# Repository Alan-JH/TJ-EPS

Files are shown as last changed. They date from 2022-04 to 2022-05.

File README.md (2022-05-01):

# TJ-EPS
Custom Battery and EPS for 2-3U Cubesat. Designed to be versatile, and to be implemented on TJ-iSPIN

Heavily inspired by the Clydespace 3G EPS, but not as expensive, and with some improvements.

## Battery
2P2S setup with 3500mAh 18650 Li-Ion cells. Voltage range from 6 to 8.4V.

Series charge balancing using BQ29209

2 Inhibits (1x ground disconnect, 1x positive disconnect)

7A Polyfuse, 8.4V input OVP, 8A Bidirectional momentary OCP/SCP

Ideal Diode with two more positive disconnect inhibits to EPS regulator input, UVP which disconnects at 6.2V falling and re-enables at 7V

One positive disconnect inhibit between EPS charge output and battery

Battery heaters and temperature telemetry to keep them above 0 deg C

Telemetry IC including Voltage, Current, SOC Charge Integration, Temperatures, and Heater control. Watchdog timer to prevent latchup.

## EPS
VBAT, 5V, 3.3V bus outputs, each with latching current limit (3A, 3A, and 5A respectively), voltage and current telemetry.

10 switchable voltage outputs, each with current and voltage telemetry, with voltage selectable between 3.3V, 5V, and BATV by jumper

Telemetry IC including all voltage and current telemetry, board temperature telemetry, and solar regulator telemetry. Watchdog timer to prevent latchup.

#### Solar Daughterboard
Daughterboard which attaches on top of the main EPS stack board.

4 solar input maximum power point tracking regulators, with two connectors each (intended for panels on opposite sides of the satellite or panels guaranteed equal sunlight).

Solar input range from 9V to 26V. Includes series diode protection on each connector. LT3652 regulators each provide up to 2A battery charging output, with 8.27V float voltage. 

Maximum power point tracking voltage settable by trim potentiometer (MUST BE SET BEFORE LAUNCH)

Input current telemetry for each individual connector, input voltage telemetry for each regulator, and output voltage and current telemetry.

## Component selection
Most components are AEC-Q100/Q101/Q200 Automotive qualified. A few important components are not, by necessity due to the chip shortage. Battery cells must be tested in house, but should be selected by brands commonly used in cubesats such as LG and Panasonic. The boards are to be tested with vibration, and vacuum with temperature cycle individually.

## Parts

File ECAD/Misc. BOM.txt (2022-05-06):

10uH: https://www.mouser.com/ProductDetail/Kyocera-AVX/LMLP07A7M100DTAS?qs=BgMWa3ErCfy790mwccrPYw%3D%3D
10uH alternate: https://www.mouser.com/ProductDetail/ABRACON/ASPI-0630HI-100M-T15?qs=bWAYEm3xoCYvNdiREkchng%3D%3D

3.3uH: https://www.mouser.com/ProductDetail/ABRACON/ASPI-0630LR-3R3M-T15?qs=bWAYEm3xoCb65F4PqHLU5A%3D%3D
3.3uH alternate: https://www.mouser.com/ProductDetail/ABRACON/ASPI-0630HI-3R3M-T15?qs=bWAYEm3xoCYwUcwgROPtBA%3D%3D

4.7uH: https://www.mouser.com/ProductDetail/ABRACON/ASPI-0630LR-4R7M-T15?qs=bWAYEm3xoCYVuRmkzS1c6A%3D%3D

33uH: https://www.mouser.com/ProductDetail/Coilcraft/XAL6060-333MEC?qs=lc2O%252BfHJPVZnUE%252BpAAaLKQ%3D%3D

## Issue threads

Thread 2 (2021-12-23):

MPPT Tracking Controller doesn't have ADC input from telemetry

Alan-JH, 2021-12-23:
Controller needs to have access to voltage and current telemetry to calculate a maximum power point

Closed 2021-12-24.

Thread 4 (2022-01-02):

Schematic TODO

Alan-JH, 2022-01-02:
- [x] Implement solar panel telemetry on separable module
- [x] Implement telemetry ADC and controls
- [x] Implement bus reset timer
- [x] Implement overcurrent retry timer
- [x] Implement STM32 Watchdog timer
- [x] Implement USB charge to MPPT4 with LTC4412
- [x] Refine component selection for Buck and Boost controllers in PCM
- [x] Make cell protections separable
- [x] Add sheet comments
- [x] Redundant capacitors (specify in component selection)

Closed 2022-01-31.

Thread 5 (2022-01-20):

Battery cell reselection

Alan-JH, 2022-01-20:
18650s with holders are too physically long
-Spot weld 18650 (High density, but impossible to safely remove cells after integration)
-18500 w/ holders (Low density, but easy to remove cells after integration)
-Pouch cell on stacked boards (Higher cost, harder to spec, and extremely similar to clydespace batt, but customizable cell protection and removeable, and denser than cylindrical cells)

Closed 2022-01-28.

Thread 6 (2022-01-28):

Consider removing destructive OVP

Alan-JH, 2022-01-28:
Semidestructive OVP involves shorting the +batt to ground in order to trigger a polyfuse, and is only a redundancy in case the charge OVP protection earlier fails.

Alan-JH, 2022-01-31:
Added redundant mosfets, and closing this for now

Closed 2022-01-31.

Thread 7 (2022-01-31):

Consolidate parts

Alan-JH, 2022-01-31:
Try to find lower part count solutions for common sub-components such as current sense and PMOS drivers. There are too many components and too little space to put them.

Alan-JH, 2022-01-31:
Going to replace LT6106 with INA180; about half the cost, more available, and less part usage

Closed 2022-03-28.

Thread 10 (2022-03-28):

Resistive heater tracks

Alan-JH, 2022-03-28:
Somehow route tracks to have 20Ohm resistance, or otherwise use PWM and capacitor to decrease power

Alan-JH, 2022-03-28:
Respec heater control mosfets

Alan-JH, 2022-03-29:
Routing 10Ohm resistance with 1V separate supply and N channel mosfets driven at 3.3V logic level

Closed 2022-03-29.

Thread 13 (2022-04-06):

Battery Heater

Alan-JH, 2022-04-06:
Consider removing 1V regulator and using longer length or smaller diameter of nichrome (60-100 ohms for 3.3V)

Pros:
Removes extra parts; removes point of failure and point of testing. Adds more contact area with battery
Cons:
Increases chance of short on 3.3V bus; heaters not isolated from rest of system

Alan-JH, 2022-04-10:
Decided on 3V3 bus

Closed 2022-04-10.

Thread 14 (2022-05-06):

Replace all connectors with JST, molex, or dupont

Alan-JH, 2022-05-06:
DF13 through hole is now obsolete

Alan-JH, 2022-05-11:
using molex picoblade

Closed 2022-05-11.

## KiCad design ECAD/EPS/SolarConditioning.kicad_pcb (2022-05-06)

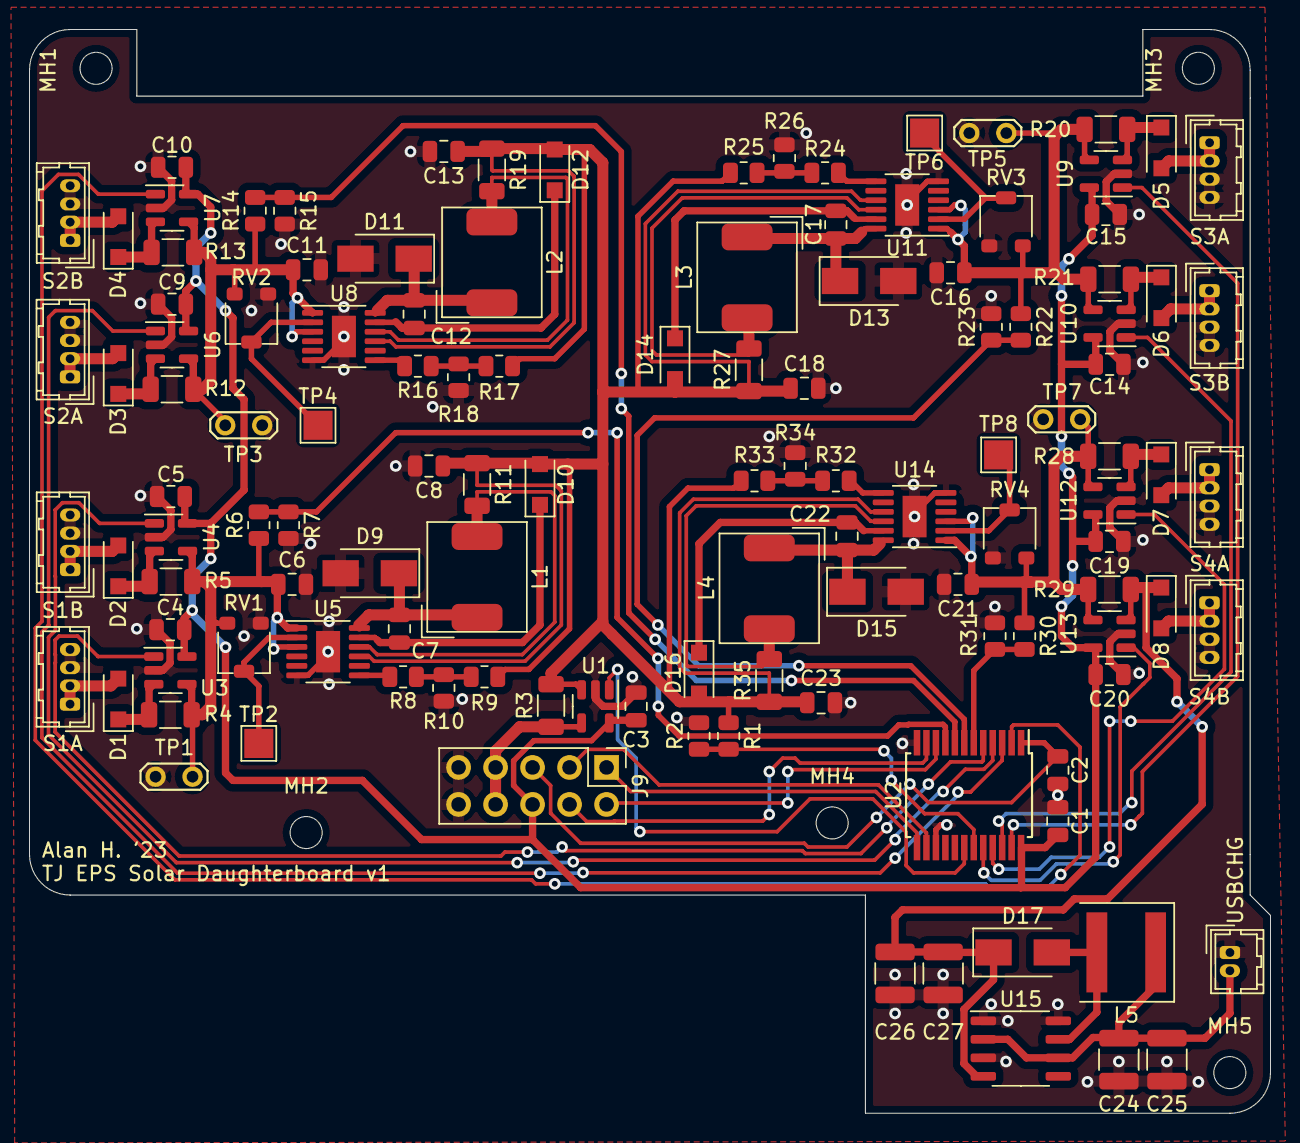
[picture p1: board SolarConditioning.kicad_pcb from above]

Board: 2 copper layers, 85.2 x 74.4 mm, 126 parts (0 on the bottom side), 69 nets.

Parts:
C1, C2, C3, C4, C5, C9, C10, C14, C15, C19, C20: 0.1uF; C_0805_2012Metric
C6, C8, C11, C13, C16, C18, C21, C23: 10uF; C_0805_2012Metric
C7, C12, C17, C22: 1uF; C_0805_2012Metric
C24, C25, C26, C27: 22uF; C_1210_3225Metric
D1, D2, D3, D4, D5, D6, D7, D8: SS34FA; D_SOD-123F
D9, D11, D13, D15, D17: CMSH3-40MA; D_SMA
D10, D12, D14, D16: RB051MM-2Y; D_SOD-123F
J1: S1A; Hirose_DF13-04P-1.25DSA_1x04_P1.25mm_Vertical
J2: S1B; Hirose_DF13-04P-1.25DSA_1x04_P1.25mm_Vertical
J3: S2A; Hirose_DF13-04P-1.25DSA_1x04_P1.25mm_Vertical
J4: S2B; Hirose_DF13-04P-1.25DSA_1x04_P1.25mm_Vertical
J5: S3A; Hirose_DF13-04P-1.25DSA_1x04_P1.25mm_Vertical
J6: S3B; Hirose_DF13-04P-1.25DSA_1x04_P1.25mm_Vertical
J7: S4A; Hirose_DF13-04P-1.25DSA_1x04_P1.25mm_Vertical
J8: S4B; Hirose_DF13-04P-1.25DSA_1x04_P1.25mm_Vertical
J9: Solar Daughterboard Connector; PinHeader_2x05_P2.54mm_Vertical
J10: USBCHG; Hirose_DF13-02P-1.25DSA_1x02_P1.25mm_Vertical
L1, L2, L3, L4: 10uH; L_AVX_LMLP07A7
L5: 33uH; L_Coilcraft_XAL60xx_6.36x6.56mm
MH1, MH2, MH3, MH4, MH5: M2; MountingHole_2.2mm_M2
R1: 200K; R_0805_2012Metric
R2: 100K; R_0805_2012Metric
R3, R4, R5, R12, R13, R20, R21, R28, R29: 4m; R_1206_3216Metric
R6, R14, R22, R30: 75K; R_0805_2012Metric
R7, R15, R23, R31: 10K; R_0805_2012Metric
R8, R16, R24, R32: 191K; R_0805_2012Metric
R9, R17, R25, R33: 147K; R_0805_2012Metric
R10, R18, R26, R34: 97.6K; R_0805_2012Metric
R11, R19, R27, R35: 50m; R_1206_3216Metric
RV1, RV2, RV3, RV4: 100K; Bourns PVG3A
TP1, TP3, TP5, TP7: VIN; TestPoint_2Pads_Pitch2.54mm_Drill0.8mm
TP2, TP4, TP6, TP8: Vmpp; TestPoint_Pad_2.0x2.0mm
U1, U3, U4, U6, U7, U9, U10, U12, U13: INA180A3; SOT-23-5
U2: CD74HC4067SM; SSOP-24_5.3x8.2mm_P0.65mm
U5, U8, U11, U14: LT3652EMSE; MSOP-12-1EP_3x4mm_P0.65mm_EP1.65x2.85mm
U15: LT1301; SO-8_3.9x4.9mm_P1.27mm

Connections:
/5VIN: C24.1, C25.1, J10.2, L5.1, U15.2 (SEL), U15.6 (VIN)
/MPPT1/A_PWR: D1.1 (K), R4.2, U3.3 (+)
/MPPT1/B_PWR: D2.1 (K), R5.2, U4.3 (+)
/MPPT1/VOUT: C8.1, C13.1, C18.1, C23.1, D10.2 (A), D12.2 (A), D14.2 (A), D16.2 (A), R1.1, R3.2, R9.2, R11.1, R17.2, R19.1, R25.2, R27.1, R33.2, R35.1, U1.3 (+), U5.9 (BAT), U8.9 (BAT), U11.9 (BAT), U14.9 (BAT)
/MPPT2/A_PWR: D3.1 (K), R12.2, U6.3 (+)
/MPPT2/B_PWR: D4.1 (K), R13.2, U7.3 (+)
/MPPT3/A_PWR: D5.1 (K), R20.2, U9.3 (+)
/MPPT3/B_PWR: D6.1 (K), R21.2, U10.3 (+)
/MPPT4/A_PWR: D7.1 (K), R28.2, U12.3 (+)
/MPPT4/B_PWR: C26.1, C27.1, D8.1 (K), D17.1 (K), R29.2, U13.3 (+), U15.4 (SENSE)
BCR_OUT: J9.7, J9.8, R3.1, U1.4 (-)
GND: C1.2, C2.2, C3.2, C4.2, C5.2, C6.2, C8.2, C9.2, C10.2, C11.2, C13.2, C14.2, C15.2, C16.2, C18.2, C19.2, C20.2, C21.2, C23.2, C24.2, C25.2, C26.2, C27.2, D9.2 (A), D11.2 (A), D13.2 (A), D15.2 (A), J1.3, J1.4, J2.3, J2.4, J3.3, J3.4, J4.3, J4.4, J5.3, J5.4, J6.3, J6.4, J7.3, J7.4, J8.3, J8.4, J9.9, J9.10, J10.1, R2.2, R7.2, R10.1, R15.2, R18.1, R23.2, R26.1, R31.2, R34.1, RV1.3, RV2.3, RV3.3, RV4.3, TP1.1, TP3.1, TP5.1, TP7.1, U1.2 (GND), U2.12 (GND), U2.15 (~E), U3.2 (GND), U4.2 (GND), U5.6 (TIMER), U5.13 (GND), U6.2 (GND), U7.2 (GND), U8.6 (TIMER), U8.13 (GND), U9.2 (GND), U10.2 (GND), U11.6 (TIMER), U11.13 (GND), U12.2 (GND), U13.2 (GND), U14.6 (TIMER), U14.13 (GND), U15.1 (GND), U15.3 (SHDN), U15.8 (PGND)
I_SA1A: U2.5 (I4), U3.1
I_SA1B: U2.4 (I5), U4.1
I_SA2A: U2.3 (I6), U6.1
I_SA2B: U2.2 (I7), U7.1
I_SA3A: U2.23 (I8), U9.1
I_SA3B: U2.22 (I9), U10.1
I_SA4A: U2.21 (I10), U12.1
I_SA4B: U2.20 (I11), U13.1
MUX3OUT: C2.1, J9.5, U2.1 (COM)
unnamed: C6.1, R4.1, R5.1, R6.1, RV1.1, TP1.2, U3.4 (-), U4.4 (-), U5.1 (VIN), U5.3 (~SHDN)
unnamed: C7.1, D9.1 (K), L1.1, U5.12 (SW)
unnamed: C7.2, D10.1 (K), U5.11 (BOOST)
unnamed: C11.1, R12.1, R13.1, R14.1, RV2.1, TP3.2, U6.4 (-), U7.4 (-), U8.1 (VIN), U8.3 (~SHDN)
unnamed: C12.1, D11.1 (K), L2.1, U8.12 (SW)
unnamed: C12.2, D12.1 (K), U8.11 (BOOST)
unnamed: C16.1, R20.1, R21.1, R22.1, RV3.1, TP5.2, U9.4 (-), U10.4 (-), U11.1 (VIN), U11.3 (~SHDN)
unnamed: C17.1, D13.1 (K), L3.1, U11.12 (SW)
unnamed: C17.2, D14.1 (K), U11.11 (BOOST)
unnamed: C21.1, R28.1, R29.1, R30.1, RV4.1, TP7.2, U12.4 (-), U13.4 (-), U14.1 (VIN), U14.3 (~SHDN)
unnamed: C22.1, D15.1 (K), L4.1, U14.12 (SW)
unnamed: C22.2, D16.1 (K), U14.11 (BOOST)
unnamed: D1.2 (A), J1.1, J1.2
unnamed: D2.2 (A), J2.1, J2.2
unnamed: D3.2 (A), J3.1, J3.2
unnamed: D4.2 (A), J4.1, J4.2
unnamed: D5.2 (A), J5.1, J5.2
unnamed: D6.2 (A), J6.1, J6.2
unnamed: D7.2 (A), J7.1, J7.2
unnamed: D8.2 (A), J8.1, J8.2
unnamed: D17.2 (A), L5.2, U15.7 (SW)
unnamed: L1.2, R11.2, U5.10 (SENSE)
unnamed: L2.2, R19.2, U8.10 (SENSE)
unnamed: L3.2, R27.2, U11.10 (SENSE)
unnamed: L4.2, R35.2, U14.10 (SENSE)
unnamed: R8.2, U5.7 (VFB)
unnamed: R8.1, R9.1, R10.2
unnamed: R16.1, R17.1, R18.2
unnamed: R16.2, U8.7 (VFB)
unnamed: R24.1, R25.1, R26.2
unnamed: R24.2, U11.7 (VFB)
unnamed: R32.1, R33.1, R34.2
unnamed: R32.2, U14.7 (VFB)
unnamed: RV1.2, TP2.1, U5.2 (VIN_REG)
unnamed: RV2.2, TP4.1, U8.2 (VIN_REG)
unnamed: RV3.2, TP6.1, U11.2 (VIN_REG)
unnamed: RV4.2, TP8.1, U14.2 (VIN_REG)
S0: J9.2, U2.10 (S0)
S1: J9.4, U2.11 (S1)
S2: J9.3, U2.14 (S2)
S3: J9.1, U2.13 (S3)
TELEM_IBCROUT: U1.1, U2.18 (I13)
TELEM_VBCROUT: R1.2, R2.1, U2.19 (I12)
VDD: C1.1, C3.1, C4.1, C5.1, C9.1, C10.1, C14.1, C15.1, C19.1, C20.1, J9.6, U1.5 (V+), U2.24 (VCC), U3.5 (V+), U4.5 (V+), U6.5 (V+), U7.5 (V+), U9.5 (V+), U10.5 (V+), U12.5 (V+), U13.5 (V+)
V_SA1: R6.2, R7.1, U2.9 (I0)
V_SA2: R14.2, R15.1, U2.8 (I1)
V_SA3: R22.2, R23.1, U2.7 (I2)
V_SA4: R30.2, R31.1, U2.6 (I3)

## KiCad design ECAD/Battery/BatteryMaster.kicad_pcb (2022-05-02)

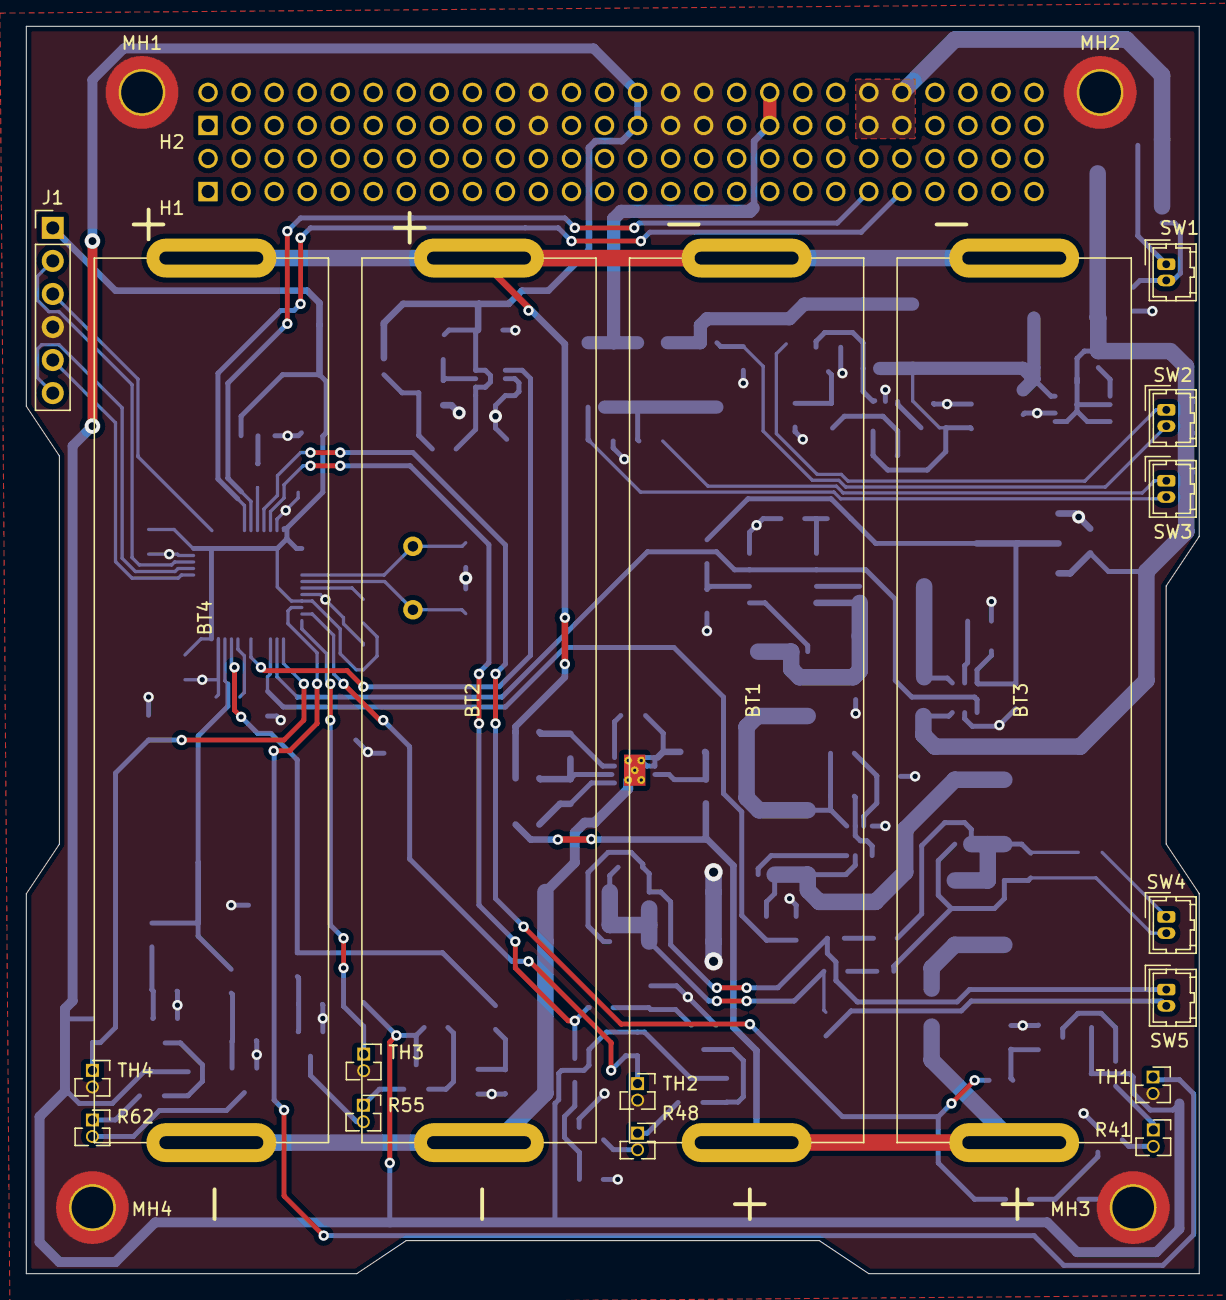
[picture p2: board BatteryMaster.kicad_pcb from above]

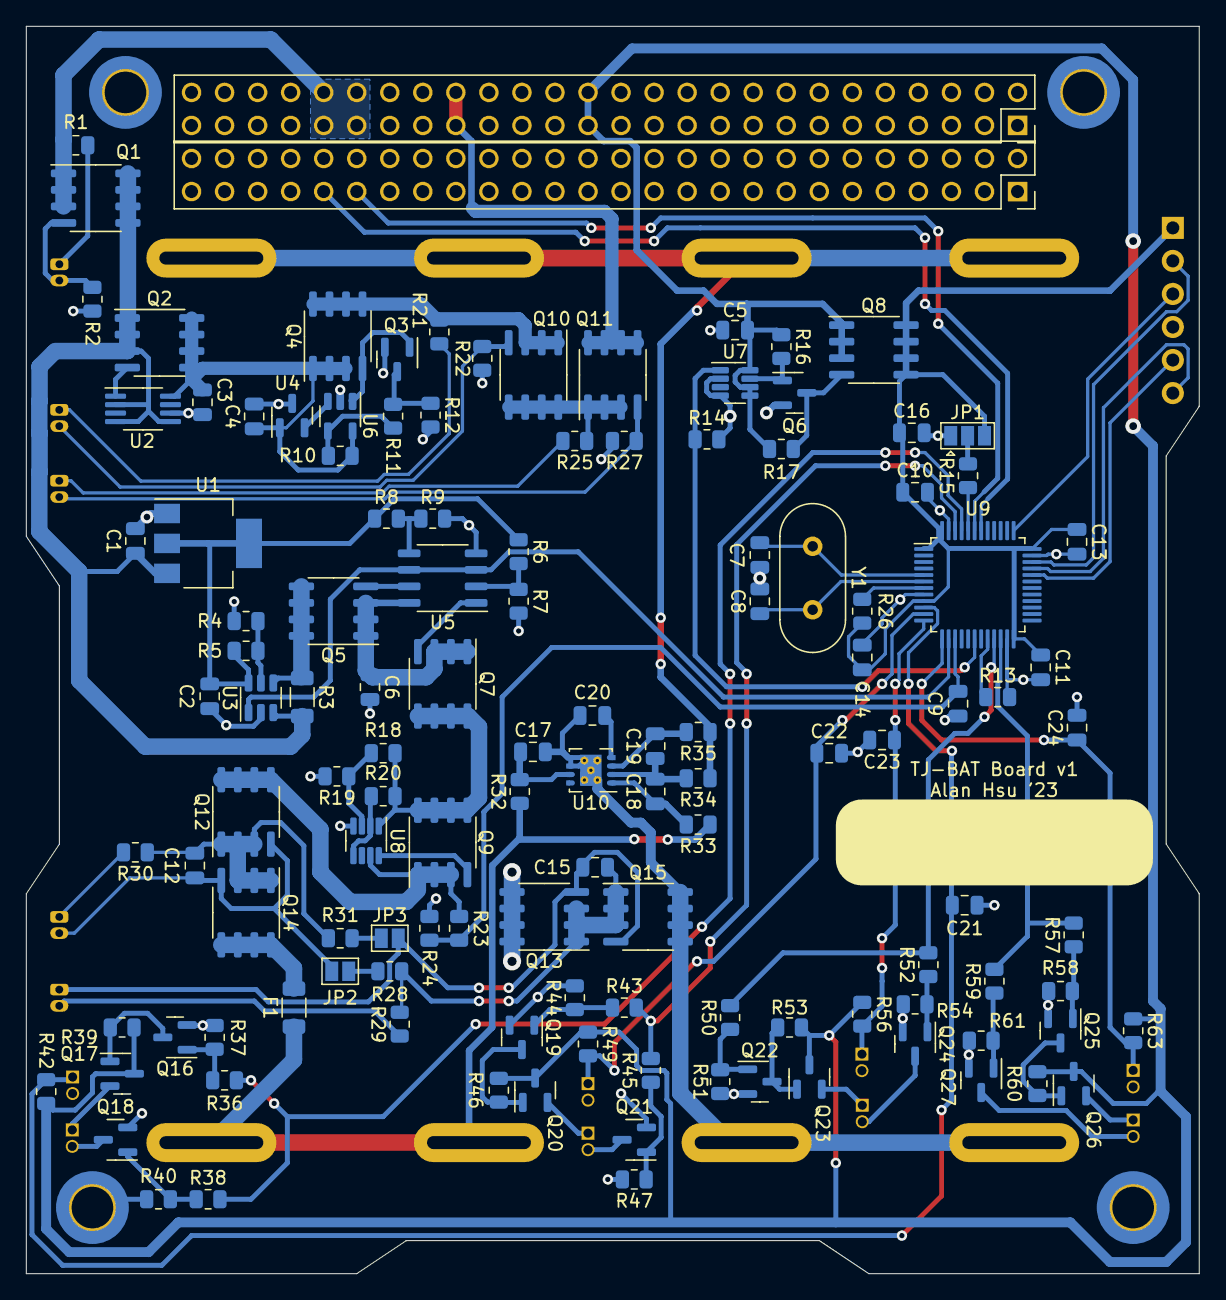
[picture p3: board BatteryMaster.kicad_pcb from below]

Board: 2 copper layers, 90.2 x 95.9 mm, 149 parts (127 on the bottom side), 97 nets.

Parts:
BT1, BT2, BT3, BT4: 18650; 18650-weld
C1, C3, C16: 10uF; C_0805_2012Metric
C2, C4, C5, C6, C9, C10, C11, C12, C13, C14, C15, C17, C18, C19, C20, C21, C22, C23, C24: 0.1uF; C_0805_2012Metric
C7, C8: 20pF; C_0805_2012Metric
F1: 7A; R_1206_3216Metric
H1, H2: Stack Header; PinSocket_2x26_P2.54mm_Vertical
J1: SWD/DEBUG; PinHeader_1x06_P2.54mm_Vertical
JP1: BOOT; SolderJumper-3_P1.3mm_Open_Pad1.0x1.5mm
JP2, JP3: LTDIS; SolderJumper-2_P1.3mm_Open_Pad1.0x1.5mm
MH1, MH2, MH3, MH4: M3; MountingHole_3.2mm_M3_DIN965_Pad_TopBottom
Q1, Q4, Q5, Q7, Q8, Q10, Q11, Q12, Q14: DMP3015LSSQ; SOIC-8_3.9x4.9mm_P1.27mm
Q2, Q9, Q13, Q15: Si4186DY; SOIC-8_3.9x4.9mm_P1.27mm
Q3, Q6, Q16, Q19, Q22, Q25: 2N7002; SOT-23
Q17, Q20, Q23, Q26: Si2371EDS-T1-BE3; SOT-23
Q18, Q21, Q24, Q27: DMG6968U-7; SOT-23
R1, R21, R25, R29, R30, R32, R35, R36, R38, R43, R45, R50, R52, R57, R59: 100R; R_0805_2012Metric
R2, R4, R5, R13, R15, R20, R22, R24, R27, R28, R31: 100K; R_0805_2012Metric
R3: 4m; R_1206_3216Metric
R6, R9: 2.49K; R_0805_2012Metric
R7, R8: 162K; R_0805_2012Metric
R10: 40K; R_0805_2012Metric
R11: 30K; R_0805_2012Metric
R12: 7.5K; R_0805_2012Metric
R14: 50K; R_0805_2012Metric
R16, R17, R26, R37, R39, R40, R44, R46, R47, R51, R53, R54, R58, R60, R61: 10K; R_0805_2012Metric
R18: 316K; R_0805_2012Metric
R19: 20K; R_0805_2012Metric
R23: 200K; R_0805_2012Metric
R33: 160R; R_0805_2012Metric
R34: 260R; R_0805_2012Metric
R41, R48, R55, R62: 80R; PinSocket_1x02_P1.27mm_Vertical
R42, R49, R56, R63: 270K; R_0805_2012Metric
SW1, SW2, SW3, SW4, SW5: INHIBIT; Hirose_DF13-02P-1.25DSA_1x02_P1.25mm_Vertical
TH1, TH2, TH3, TH4: 100K NTC; PinSocket_1x02_P1.27mm_Vertical
U1: LM1117-3.3; SOT-223-3_TabPin2
U2: LTC4359-MS8; MSOP-8_3x3mm_P0.65mm
U3: INA181A2; SOT-23-6
U4: MAX6035xxUR30; SOT-23
U5: LM358; SO-8_3.9x4.9mm_P1.27mm
U6: TLV9361IDBVR; SOT-23-5
U7: MAX6369; SOT-23-8
U8: LTC4365TS8-1; TSOT-23-8
U9: STM32F103C8Tx; LQFP-48_7x7mm_P0.5mm
U10: BQ29209; Texas_S-PVSON-N8_ThermalVias
Y1: 8MHz; Crystal_HC49-4H_Vertical

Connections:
+3.3VA: C2.1, R5.2, R6.1, R8.1, U1.2 (VO), U3.6 (V+)
+3V3: C5.1, H2.27, H2.28, Q8.1 (S), Q8.2 (S), Q8.3 (S), Q17.3 (D), Q20.3 (D), Q23.3 (D), Q26.3 (D), R16.1, R17.1, R39.1, R42.1, R46.1, R49.1, R53.1, R56.1, R60.1, R63.1, U7.5 (SET1), U7.6 (SET2), U7.8 (VCC)
+5V: H2.25, H2.26
+BATT: H2.45, H2.46
-BATT: BT2.2 (-), BT4.2 (-), C17.2, C20.2, Q15.5 (D), Q15.6 (D), Q15.7 (D), Q15.8 (D), U10.5 (GND), U10.6 (~CB_EN), U10.9 (PGND)
/BOOT0: R15.1, U9.44 (BOOT0)
/BOOT1: R13.1, U9.20 (PB2)
/D+: J1.6, U9.33 (PA12)
/D-: J1.5, U9.32 (PA11)
/H1CTRL: R36.2, R38.2, U9.45 (PB8)
/H2CTRL: R43.2, R45.2, U9.46 (PB9)
/H3CTRL: R50.2, R52.2, U9.21 (PB10)
/H4CTRL: R57.2, R59.2, U9.22 (PB11)
/HANDSHAKE: R14.1, U7.1 (WDI), U9.18 (PB0)
/RESET: R26.2, U9.7 (NRST)
/SCL: H1.43, U9.42 (PB6)
/SDA: H1.41, U9.43 (PB7)
/SWDCLK: J1.3, U9.37 (PA14)
/SWDIO: J1.2, U9.34 (PA13)
/TBAT1: C21.1, R42.2, TH1.1, U9.10 (PA0)
/TBAT2: C22.1, R49.2, TH2.1, U9.11 (PA1)
/TBAT3: C23.1, R56.2, TH3.1, U9.12 (PA2)
/TBAT4: C24.1, R63.2, TH4.1, U9.13 (PA3)
/TELEM_IBAT: U3.1, U5.3 (+), U5.6 (-), U9.14 (PA4)
/TELEM_VBAT: C9.1, R23.2, R24.1, U9.15 (PA5)
BCR_OUT: H2.41, H2.42, H2.43, H2.44, Q1.1 (S), Q1.2 (S), Q1.3 (S), R1.1
GND: C1.2, C2.2, C3.2, C4.2, C5.2, C6.2, C7.2, C8.2, C9.2, C10.2, C11.2, C13.2, C14.2, C16.2, C21.2, C22.2, C23.2, C24.2, H2.21, H2.22, H2.29, H2.30, H2.31, H2.32, J1.4, JP1.1 (A), MH1.1, MH2.1, MH3.1, MH4.1, Q3.2 (S), Q6.2 (S), Q13.5 (D), Q13.6 (D), Q13.7 (D), Q13.8 (D), Q16.2 (S), Q18.2 (S), Q19.2 (S), Q21.2 (S), Q22.2 (S), Q24.2 (S), Q25.2 (S), Q27.2 (S), R2.2, R4.2, R7.2, R9.2, R12.2, R13.2, R14.2, R19.2, R22.2, R24.2, R27.2, R37.2, R40.2, R44.2, R47.2, R51.2, R54.2, R58.2, R61.2, TH1.2, TH2.2, TH3.2, TH4.2, U1.1 (GND), U2.6 (Vss), U3.2 (GND), U4.3 (GND), U5.4 (V-), U6.2 (V-), U7.2 (GND), U7.4 (SET0), U8.4 (GND), U9.8 (VSSA), U9.23 (VSS), U9.35 (VSS), U9.47 (VSS)
unnamed: BT1.1 (+), BT3.1 (+), F1.1, R32.1, R33.1
unnamed: BT1.2 (-), BT2.1 (+), BT3.2 (-), BT4.1 (+), R34.1, R35.1
unnamed: C1.1, Q1.5 (D), Q1.6 (D), Q1.7 (D), Q1.8 (D), Q2.1 (S), Q2.2 (S), Q2.3 (S), R3.2, U1.3 (VI), U2.2 (SRC), U2.4 (IN), U2.5 (~SHDN), U3.3 (+)
unnamed: C3.1, C4.1, Q2.5 (D), Q2.6 (D), Q2.7 (D), Q2.8 (D), Q4.1 (S), Q4.2 (S), Q4.3 (S), R10.1, U2.8 (OUT), U4.1 (IN), U6.5 (V+)
unnamed: C6.1, Q5.1 (S), Q5.2 (S), Q5.3 (S), Q7.1 (S), Q7.2 (S), Q7.3 (S), U5.8 (V+)
unnamed: C7.1, U9.5 (PD0), Y1.1
unnamed: C8.1, U9.6 (PD1), Y1.2
unnamed: C12.1, Q12.1 (S), Q12.2 (S), Q12.3 (S), Q14.1 (S), Q14.2 (S), Q14.3 (S), R30.1, R31.1
unnamed: C12.2, JP2.1, Q12.4 (G), Q14.4 (G), SW4.2 (B)
unnamed: C15.1, JP3.2, Q13.4 (G), Q15.4 (G), SW5.1 (A)
unnamed: C15.2, Q13.1 (S), Q13.2 (S), Q13.3 (S), Q15.1 (S), Q15.2 (S), Q15.3 (S), R28.2, R29.2
unnamed: C17.1, R32.2, U10.7 (VDD)
unnamed: C18.1, R33.2, U10.1 (VC2)
unnamed: C18.2, C19.1, R34.2, U10.2 (VC1)
unnamed: C19.2, R35.2, U10.3 (VC1_CB)
unnamed: C20.1, U10.4 (CD)
unnamed: F1.2, Q14.5 (D), Q14.6 (D), Q14.7 (D), Q14.8 (D)
unnamed: JP1.2 (C), R15.2
unnamed: JP2.2, R28.1
unnamed: JP3.1, R31.2
unnamed: Q1.4 (G), R2.1, SW1.2 (B)
unnamed: Q2.4 (G), U2.1 (GATE)
unnamed: Q3.1 (G), Q4.4 (G), U6.1
unnamed: Q3.3 (D), R11.2, R12.1
unnamed: Q5.4 (G), U5.7
unnamed: Q5.5 (D), Q5.6 (D), Q5.7 (D), Q5.8 (D), R3.1, U3.4 (-)
unnamed: Q6.1 (G), R16.2, U7.7 (~WDO)
unnamed: Q6.3 (D), Q8.4 (G), R17.2
unnamed: Q7.4 (G), U5.1
unnamed: Q7.5 (D), Q7.6 (D), Q7.7 (D), Q7.8 (D), Q9.5 (D), Q9.6 (D), Q9.7 (D), Q9.8 (D), R18.1, R20.1, U8.1 (Vin)
unnamed: Q9.4 (G), U8.8 (GATE)
unnamed: Q4.5 (D), Q4.6 (D), Q4.7 (D), Q4.8 (D), Q10.1 (S), Q10.2 (S), Q10.3 (S), R21.1
unnamed: Q10.4 (G), R22.1, SW2.2 (B)
unnamed: Q10.5 (D), Q10.6 (D), Q10.7 (D), Q10.8 (D), Q11.1 (S), Q11.2 (S), Q11.3 (S), R25.1
unnamed: Q11.4 (G), R27.1, SW3.2 (B)
unnamed: Q9.1 (S), Q9.2 (S), Q9.3 (S), Q12.5 (D), Q12.6 (D), Q12.7 (D), Q12.8 (D), R23.1, U8.7 (Vout)
unnamed: Q16.1 (G), R36.1, R37.1
unnamed: Q16.3 (D), Q17.1 (G), R39.2
unnamed: Q17.2 (S), R41.1
unnamed: Q18.1 (G), R38.1, R40.1
unnamed: Q18.3 (D), R41.2
unnamed: Q19.1 (G), R43.1, R44.1
unnamed: Q19.3 (D), Q20.1 (G), R46.2
unnamed: Q20.2 (S), R48.1
unnamed: Q21.1 (G), R45.1, R47.1
unnamed: Q21.3 (D), R48.2
unnamed: Q22.1 (G), R50.1, R51.1
unnamed: Q22.3 (D), Q23.1 (G), R53.2
unnamed: Q23.2 (S), R55.1
unnamed: Q24.1 (G), R52.1, R54.1
unnamed: Q24.3 (D), R55.2
unnamed: Q25.1 (G), R57.1, R58.1
unnamed: Q25.3 (D), Q26.1 (G), R60.2
unnamed: Q26.2 (S), R62.1
unnamed: Q27.1 (G), R59.1, R61.1
unnamed: Q27.3 (D), R62.2
unnamed: R1.2, SW1.1 (A)
unnamed: R4.1, R5.1, U3.5 (REF)
unnamed: R6.2, R7.1, U5.2 (-)
unnamed: R8.2, R9.1, U5.5 (+)
unnamed: R10.2, R11.1, U6.4 (-)
unnamed: R18.2, R19.1, U8.3 (OV)
unnamed: R20.2, U8.2 (UV), U8.5 (~SHDN)
unnamed: R21.2, SW2.1 (A)
unnamed: R25.2, SW3.1 (A)
unnamed: R29.1, SW5.2 (B)
unnamed: R30.2, SW4.1 (A)
unnamed: U4.2 (OUT), U6.3 (+)
PCM_IN: H2.35, H2.36, Q11.5 (D), Q11.6 (D), Q11.7 (D), Q11.8 (D)
VDD: C10.1, C11.1, C13.1, C14.1, C16.1, J1.1, JP1.3 (B), Q8.5 (D), Q8.6 (D), Q8.7 (D), Q8.8 (D), R26.1, U9.1 (VBAT), U9.9 (VDDA), U9.24 (VDD), U9.36 (VDD), U9.48 (VDD)

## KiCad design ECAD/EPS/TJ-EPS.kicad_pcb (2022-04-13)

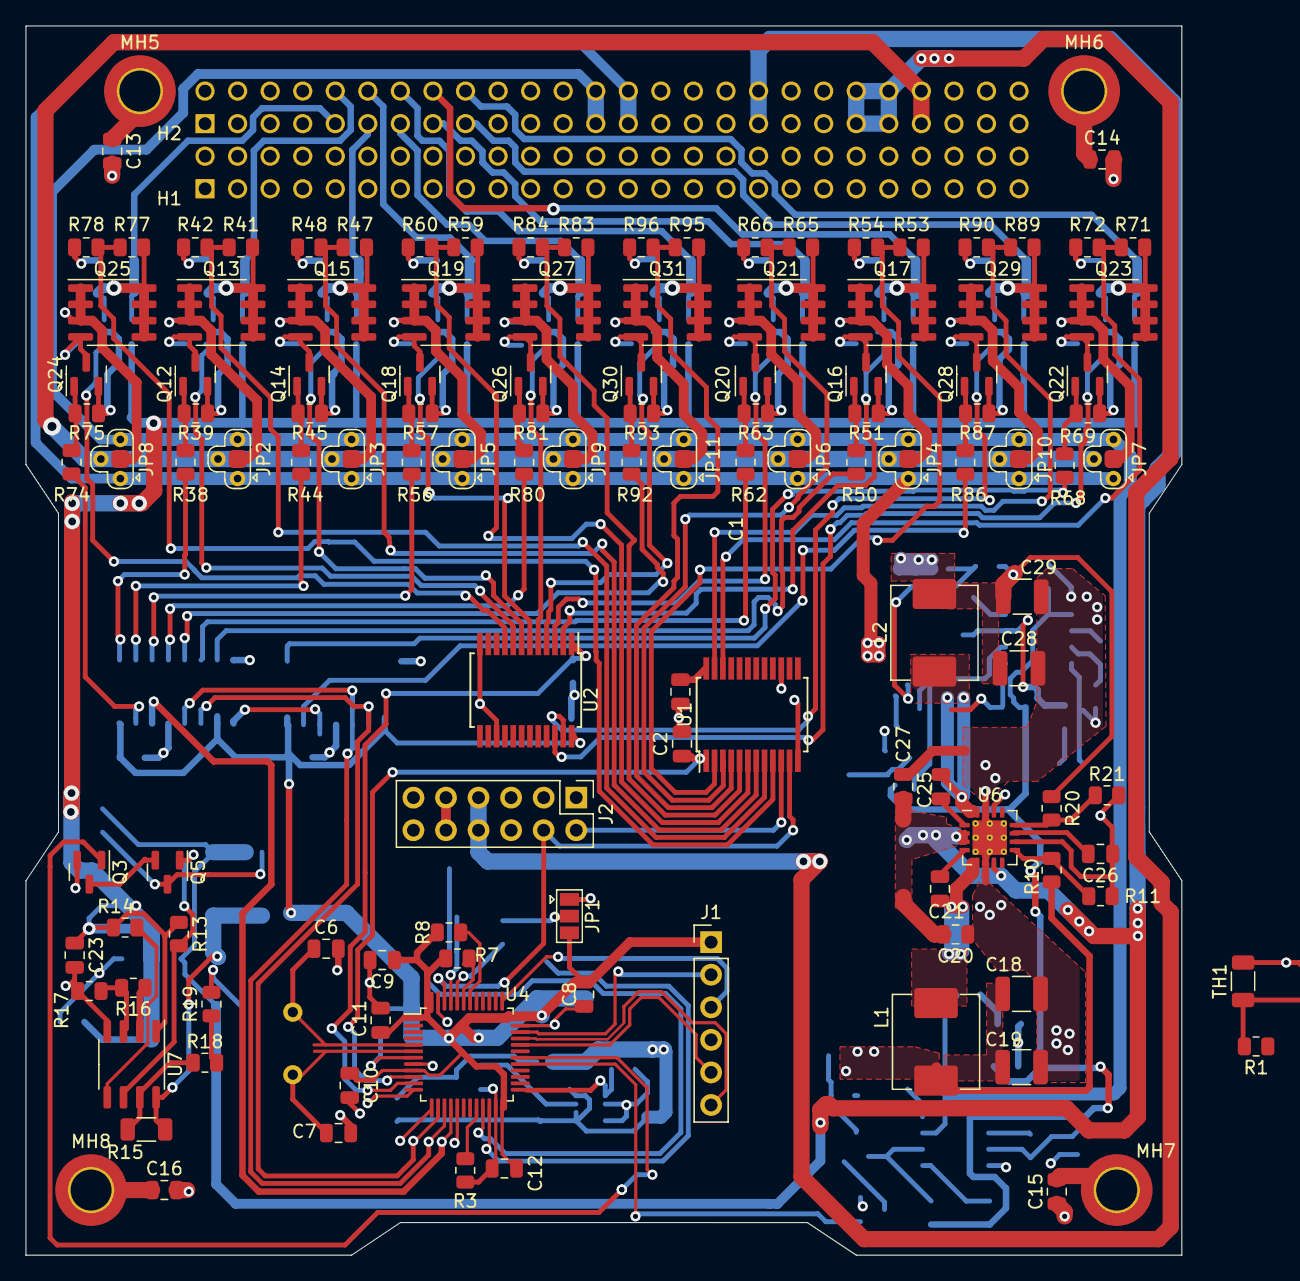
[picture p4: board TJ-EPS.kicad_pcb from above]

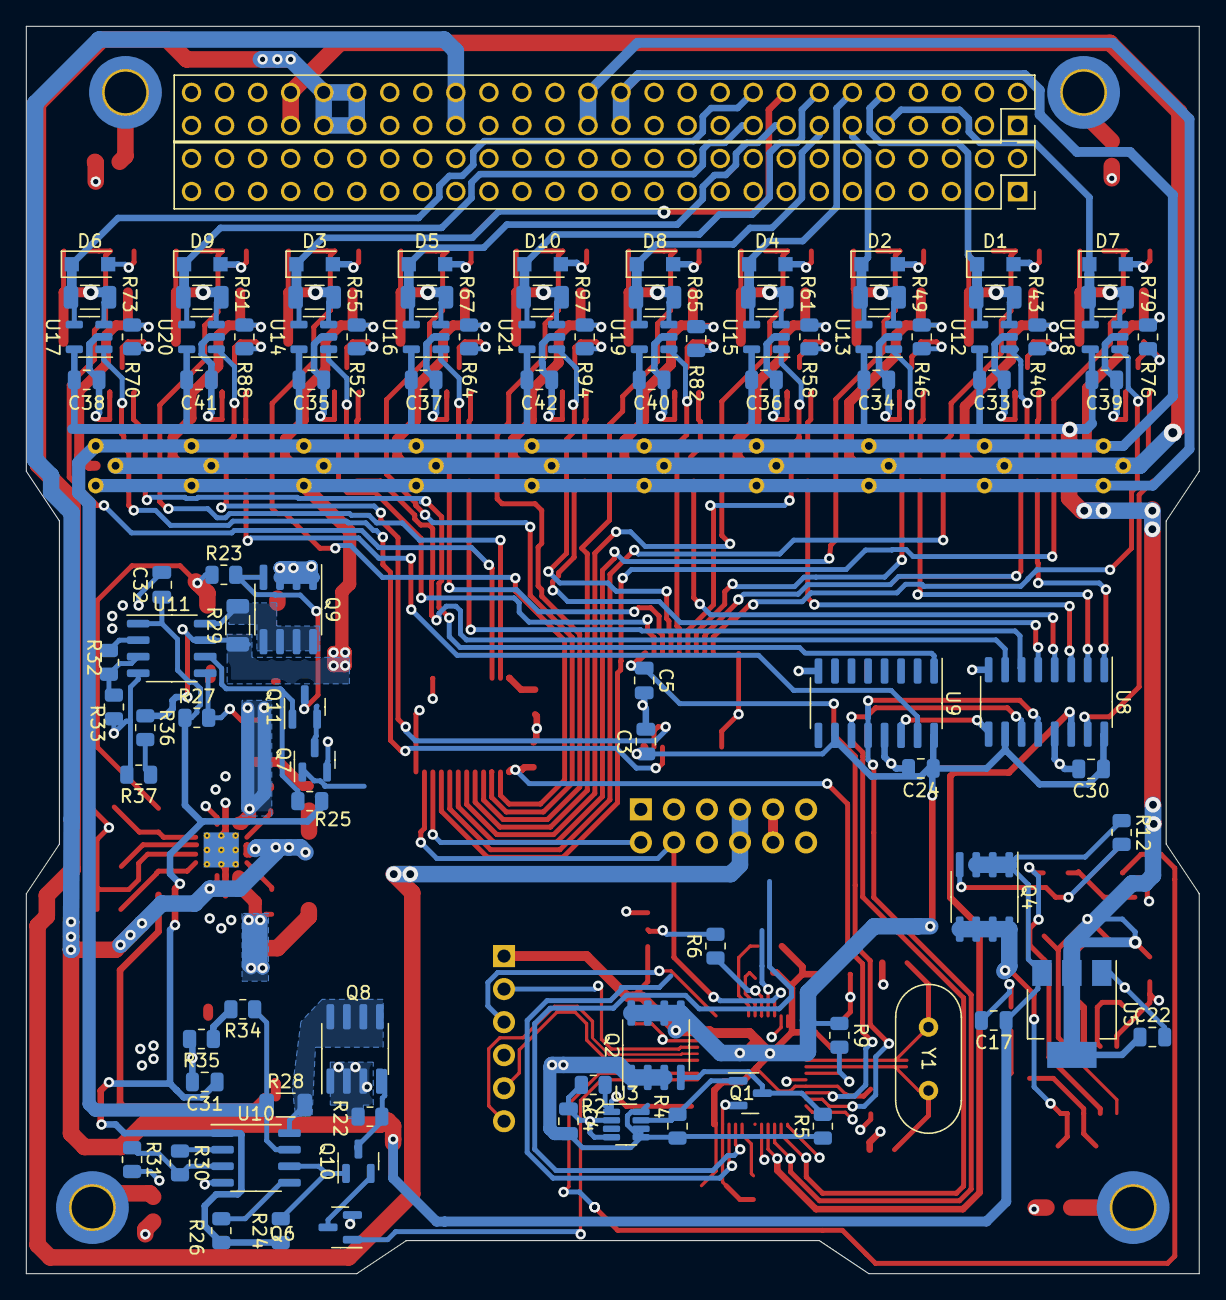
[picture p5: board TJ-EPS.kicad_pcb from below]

Board: 4 copper layers, 90.2 x 95.9 mm, 228 parts (99 on the bottom side), 157 nets.

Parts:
C1, C3, C4, C8, C9, C10, C11, C13, C14, C15, C16, C21, C23, C24, C25, C30, C31, C32, C33, C34, C35, C36, C37, C38, C39, C40, C41, C42: 0.1uF; C_0805_2012Metric
C2, C5: 0.01uF; C_0805_2012Metric
C6, C7: 20pF; C_0805_2012Metric
C12, C17, C20, C22, C27: 10uF; C_0805_2012Metric
C18, C19, C28, C29: 22uF; C_1210_3225Metric
C26: 1uF; C_0805_2012Metric
D1, D2, D3, D4, D5, D6, D7, D8, D9, D10: RR264MM; D_SOD-123F
H1: Stack Header 2; PinSocket_2x26_P2.54mm_Vertical
H2: Stack Header 1; PinSocket_2x26_P2.54mm_Vertical
J1: SWD/DEBUG; PinHeader_1x06_P2.54mm_Vertical
J2: Solar Daughterboard Connector; PinHeader_2x06_P2.54mm_Vertical
JP1: BOOT; SolderJumper-3_P1.3mm_Open_Pad1.0x1.5mm
JP2, JP3, JP4, JP5, JP6, JP7, JP8, JP9, JP10, JP11: JP; SolderJumper-4_P1.3mm_Open_RoundedPad1.0x1.5mm
L1: 4.7uH; L_Abracon_ASPI-0630LR
L2: 3.3uH; L_Abracon_ASPI-0630LR
MH1, MH2, MH3, MH4: M2.5; MountingHole_2.7mm_M2.5
MH5, MH6, MH7, MH8: M3; MountingHole_3.2mm_M3_DIN965_Pad_TopBottom
Q1, Q3, Q5, Q6, Q7, Q10, Q11, Q12, Q14, Q16, Q18, Q20, Q22, Q24, Q26, Q28, Q30: 2N7002; SOT-23
Q2, Q4, Q8, Q9, Q13, Q15, Q17, Q19, Q21, Q23, Q25, Q27, Q29, Q31: IRF7458; SOIC-8_3.9x4.9mm_P1.27mm
R1: 270K; R_0805_2012Metric
R2: 50K; R_0805_2012Metric
R3, R6, R19, R34, R35, R36, R37, R42, R48, R54, R60, R66, R72, R78, R84, R90, R96: 100K; R_0805_2012Metric
R4, R5, R9, R12, R13, R14, R22, R23, R24, R25, R26, R27, R39, R40, R45, R46, R51, R52, R57, R58, R63, R64, R69, R70, R75, R76, R81, R82, R87, R88, R93, R94: 10K; R_0805_2012Metric
R7, R8: 2.2K; R_0805_2012Metric
R10: 124K; R_0805_2012Metric
R11, R21: 22.1K; R_0805_2012Metric
R15, R28, R29: 10m; R_1206_3216Metric
R16: 9.5K; R_0805_2012Metric
R17: 3K; R_0805_2012Metric
R18, R41, R47, R53, R59, R65, R71, R77, R83, R89, R95: 200K; R_0805_2012Metric
R20: 73.2K; R_0805_2012Metric
R30, R32: 6K; R_0805_2012Metric
R31, R33: 4K; R_0805_2012Metric
R38, R44, R50, R56, R62, R68, R74, R80, R86, R92: 100R; R_0805_2012Metric
R43, R49, R55, R61, R67, R73, R79, R85, R91, R97: 4m; R_1206_3216Metric
TH1: 100K NTC; R_1206_3216Metric
U1, U2: CD74HC4067SM; SSOP-24_5.3x8.2mm_P0.65mm
U3: MAX6369; SOT-23-8
U4: STM32F103C8Tx; LQFP-48_7x7mm_P0.5mm
U5: LM1117-3.3; SOT-223-3_TabPin2
U6: TPS54394RSAR; Texas_S-PVQFN-N16_EP2.7x2.7mm_ThermalVias
U7, U10, U11: MAX4373F; SO-8_3.9x4.9mm_P1.27mm
U8, U9: 74HC595; SOIC-16_3.9x9.9mm_P1.27mm
U12, U13, U14, U15, U16, U17, U18, U19, U20, U21: INA180A3; SOT-23-5
Y1: 8MHz; Crystal_HC49-4H_Vertical

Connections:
+3.3VA: C4.1, C28.1, C29.1, L2.2, Q2.1 (S), Q2.2 (S), Q2.3 (S), Q9.1 (S), Q9.2 (S), Q9.3 (S), R4.1, R5.1, R20.1, R23.1, U3.5 (SET1), U3.6 (SET2), U3.8 (VCC)
+3V3: H2.27, H2.28, JP2.1 (A), JP3.1 (A), JP4.1 (A), JP5.1 (A), JP6.1 (A), JP7.1 (A), JP8.1 (A), JP9.1 (A), JP10.1 (A), JP11.1 (A), R1.1, R29.1, R36.1, U11.7 (RS-)
+5V: H2.25, H2.26, JP2.3 (B), JP3.3 (B), JP4.3 (B), JP5.3 (B), JP6.3 (B), JP7.3 (B), JP8.3 (B), JP9.3 (B), JP10.3 (B), JP11.3 (B), R28.1, R34.1, U10.7 (RS-)
+BATT: H2.45, H2.46, JP2.4 (D), JP3.4 (D), JP4.4 (D), JP5.4 (D), JP6.4 (D), JP7.4 (D), JP8.4 (D), JP9.4 (D), JP10.4 (D), JP11.4 (D), R15.1, R18.1, U7.7 (RS-)
/BOOT0: R6.1, U4.44 (BOOT0)
/BOOT1: R3.1, U4.20 (PB2)
/D+: J1.6, U4.33 (PA12)
/D-: J1.5, U4.32 (PA11)
/HANDSHAKE: R2.1, U3.1 (WDI), U4.25 (PB12)
/RESET: R9.2, U4.7 (NRST)
/SCL: H1.43, R8.2, U4.42 (PB6)
/SDA: H1.41, R7.2, U4.43 (PB7)
/SWDCLK: J1.3, U4.37 (PA14)
/SWDIO: J1.2, U4.34 (PA13)
BCR_OUT: H2.41, H2.42, H2.43, H2.44, J2.7, J2.8
GND: C1.2, C2.2, C3.2, C4.2, C5.2, C6.2, C7.2, C8.2, C9.2, C10.2, C11.2, C12.2, C13.2, C14.2, C15.2, C16.2, C17.2, C18.2, C19.2, C20.1, C22.2, C23.2, C24.2, C26.1, C27.1, C28.2, C29.2, C30.2, C31.2, C32.2, C33.2, C34.2, C35.2, C36.2, C37.2, C38.2, C39.2, C40.2, C41.2, C42.2, D1.2 (A), D2.2 (A), D3.2 (A), D4.2 (A), D5.2 (A), D6.2 (A), D7.2 (A), D8.2 (A), D9.2 (A), D10.2 (A), H2.21, H2.22, H2.29, H2.30, H2.31, H2.32, J1.4, J2.11, J2.12, JP1.1 (A), Q1.2 (S), Q3.2 (S), Q6.2 (S), Q7.2 (S), Q12.2 (S), Q14.2 (S), Q16.2 (S), Q18.2 (S), Q20.2 (S), Q22.2 (S), Q24.2 (S), Q26.2 (S), Q28.2 (S), Q30.2 (S), R2.2, R3.2, R11.2, R17.2, R19.2, R21.2, R31.2, R33.2, R35.2, R37.2, R39.2, R42.2, R45.2, R48.2, R51.2, R54.2, R57.2, R60.2, R63.2, R66.2, R69.2, R72.2, R75.2, R78.2, R81.2, R84.2, R87.2, R90.2, R93.2, R96.2, TH1.2, U1.12 (GND), U1.15 (~E), U2.12 (GND), U2.15 (~E), U3.2 (GND), U3.4 (SET0), U4.8 (VSSA), U4.23 (VSS), U4.35 (VSS), U4.47 (VSS), U5.1 (GND), U6.6 (PGND1), U6.10 (GND), U6.15 (PGND2), U6.17 (PADGND), U7.4 (GND), U8.8 (GND), U8.13 (~OE), U9.8 (GND), U9.13 (~OE), U10.4 (GND), U11.4 (GND), U12.2 (GND), U13.2 (GND), U14.2 (GND), U15.2 (GND), U16.2 (GND), U17.2 (GND), U18.2 (GND), U19.2 (GND), U20.2 (GND), U21.2 (GND)
MUX1OUT: C2.1, U1.1 (COM), U4.10 (PA0)
MUX2OUT: C5.1, U2.1 (COM), U4.11 (PA1)
MUX3OUT: J2.5, U4.12 (PA2)
MUX4OUT: J2.6, U4.13 (PA3)
unnamed: C6.1, U4.5 (PD0), Y1.1
unnamed: C7.1, U4.6 (PD1), Y1.2
unnamed: C13.1, MH5.1
unnamed: C14.1, MH6.1
unnamed: C15.1, MH7.1
unnamed: C16.1, MH8.1
unnamed: C18.1, C19.1, L1.1, Q8.1 (S), Q8.2 (S), Q8.3 (S), R10.1, R22.1
unnamed: C21.1, U6.4 (VBST1)
unnamed: C21.2, L1.2, U6.5 (SW1)
unnamed: C25.1, U6.1 (VBST2)
unnamed: C25.2, L2.1, U6.16 (SW2)
unnamed: C26.2, U6.11 (VREG5)
unnamed: JP1.2 (C), R6.2
unnamed: JP2.2 (C), Q13.1 (S), Q13.2 (S), Q13.3 (S), R40.1
unnamed: JP3.2 (C), Q15.1 (S), Q15.2 (S), Q15.3 (S), R46.1
unnamed: JP4.2 (C), Q17.1 (S), Q17.2 (S), Q17.3 (S), R52.1
unnamed: JP5.2 (C), Q19.1 (S), Q19.2 (S), Q19.3 (S), R58.1
unnamed: JP6.2 (C), Q21.1 (S), Q21.2 (S), Q21.3 (S), R64.1
unnamed: JP7.2 (C), Q23.1 (S), Q23.2 (S), Q23.3 (S), R70.1
unnamed: JP8.2 (C), Q25.1 (S), Q25.2 (S), Q25.3 (S), R76.1
unnamed: JP9.2 (C), Q27.1 (S), Q27.2 (S), Q27.3 (S), R82.1
unnamed: JP10.2 (C), Q29.1 (S), Q29.2 (S), Q29.3 (S), R88.1
unnamed: JP11.2 (C), Q31.1 (S), Q31.2 (S), Q31.3 (S), R94.1
unnamed: Q1.1 (G), R4.2, U3.7 (~WDO)
unnamed: Q1.3 (D), Q2.4 (G), R5.2
unnamed: Q3.3 (D), Q5.2 (S)
unnamed: Q4.4 (G), Q5.3 (D), R12.2
unnamed: Q4.5 (D), Q4.6 (D), Q4.7 (D), Q4.8 (D), R15.2, U7.8 (RS+)
unnamed: Q5.1 (G), R13.2, U7.6 (COUT1)
unnamed: Q8.5 (D), Q8.6 (D), Q8.7 (D), Q8.8 (D), R28.2, U10.8 (RS+)
unnamed: Q9.5 (D), Q9.6 (D), Q9.7 (D), Q9.8 (D), R29.2, U11.8 (RS+)
unnamed: Q10.1 (G), R24.2, U10.6 (COUT1)
unnamed: Q6.3 (D), Q10.2 (S)
unnamed: Q8.4 (G), Q10.3 (D), R22.2
unnamed: Q11.1 (G), R25.2, U11.6 (COUT1)
unnamed: Q7.3 (D), Q11.2 (S)
unnamed: Q9.4 (G), Q11.3 (D), R23.2
unnamed: Q12.1 (G), R38.1, R39.1
unnamed: Q12.3 (D), Q13.4 (G), R40.2
unnamed: Q13.5 (D), Q13.6 (D), Q13.7 (D), Q13.8 (D), R41.1, R43.2, U12.3 (+)
unnamed: Q14.1 (G), R44.1, R45.1
unnamed: Q14.3 (D), Q15.4 (G), R46.2
unnamed: Q15.5 (D), Q15.6 (D), Q15.7 (D), Q15.8 (D), R47.1, R49.2, U13.3 (+)
unnamed: Q16.1 (G), R50.1, R51.1
unnamed: Q16.3 (D), Q17.4 (G), R52.2
unnamed: Q17.5 (D), Q17.6 (D), Q17.7 (D), Q17.8 (D), R53.1, R55.2, U14.3 (+)
unnamed: Q18.1 (G), R56.1, R57.1
unnamed: Q18.3 (D), Q19.4 (G), R58.2
unnamed: Q19.5 (D), Q19.6 (D), Q19.7 (D), Q19.8 (D), R59.1, R61.2, U15.3 (+)
unnamed: Q20.1 (G), R62.1, R63.1
unnamed: Q20.3 (D), Q21.4 (G), R64.2
unnamed: Q21.5 (D), Q21.6 (D), Q21.7 (D), Q21.8 (D), R65.1, R67.2, U16.3 (+)
unnamed: Q22.1 (G), R68.1, R69.1
unnamed: Q22.3 (D), Q23.4 (G), R70.2
unnamed: Q23.5 (D), Q23.6 (D), Q23.7 (D), Q23.8 (D), R71.1, R73.2, U17.3 (+)
unnamed: Q24.1 (G), R74.1, R75.1
unnamed: Q24.3 (D), Q25.4 (G), R76.2
unnamed: Q25.5 (D), Q25.6 (D), Q25.7 (D), Q25.8 (D), R77.1, R79.2, U18.3 (+)
unnamed: Q26.1 (G), R80.1, R81.1
unnamed: Q26.3 (D), Q27.4 (G), R82.2
unnamed: Q27.5 (D), Q27.6 (D), Q27.7 (D), Q27.8 (D), R83.1, R85.2, U19.3 (+)
unnamed: Q28.1 (G), R86.1, R87.1
unnamed: Q28.3 (D), Q29.4 (G), R88.2
unnamed: Q29.5 (D), Q29.6 (D), Q29.7 (D), Q29.8 (D), R89.1, R91.2, U20.3 (+)
unnamed: Q30.1 (G), R92.1, R93.1
unnamed: Q30.3 (D), Q31.4 (G), R94.2
unnamed: Q31.5 (D), Q31.6 (D), Q31.7 (D), Q31.8 (D), R95.1, R97.2, U21.3 (+)
unnamed: R10.2, R11.1, U6.9 (VFB1)
unnamed: R16.2, R17.1, U7.3 (CIN1)
unnamed: R20.2, R21.1, U6.12 (VFB2)
unnamed: R30.2, R31.1, U10.3 (CIN1)
unnamed: R32.2, R33.1, U11.3 (CIN1)
unnamed: U8.9 (QH'), U9.14 (SER)
PCM_IN: C17.1, C20.2, C27.2, H2.35, H2.36, Q4.1 (S), Q4.2 (S), Q4.3 (S), R12.1, U5.3 (VI), U6.2 (VIN2), U6.3 (VIN1), U6.7 (EN1), U6.14 (EN2)
RST3V3: Q7.1 (G), U4.17 (PA7)
RST3V3OCP: R27.2, U4.28 (PB15), U11.5 (~RESET)
RST5V: Q6.1 (G), U4.29 (PA8)
RST5VOCP: R26.2, U4.27 (PB14), U10.5 (~RESET)
RSTBATV: Q3.1 (G), U4.30 (PA9)
RSTBATVOCP: R14.2, U4.26 (PB13), U7.5 (~RESET)
S0: J2.2, U1.10 (S0), U2.10 (S0), U4.45 (PB8)
S1: J2.4, U1.11 (S1), U2.11 (S1), U4.46 (PB9)
S2: J2.3, U1.14 (S2), U2.14 (S2), U4.21 (PB10)
S3: J2.1, U1.13 (S3), U2.13 (S3), U4.22 (PB11)
SRCLK: U4.14 (PA4), U8.11 (SRCLK), U9.11 (SRCLK)
SRLCH: U4.15 (PA5), U8.12 (RCLK), U9.12 (RCLK)
SRSERIN: U4.16 (PA6), U8.14 (SER)
SW1: D7.1 (K), H2.9, R79.1, U18.4 (-)
SW1GATE: R74.2, U8.15 (QA)
SW2: D1.1 (K), H2.10, R43.1, U12.4 (-)
SW2GATE: R38.2, U8.1 (QB)
SW3: D2.1 (K), H2.11, R49.1, U13.4 (-)
SW3GATE: R44.2, U8.2 (QC)
SW4: D4.1 (K), H2.12, R61.1, U15.4 (-)
SW4GATE: R56.2, U8.3 (QD)
SW5: D8.1 (K), H2.13, R85.1, U19.4 (-)
SW5GATE: R80.2, U8.4 (QE)
SW6: D10.1 (K), H2.14, R97.1, U21.4 (-)
SW6GATE: R92.2, U8.5 (QF)
SW7: D5.1 (K), H2.15, R67.1, U16.4 (-)
SW7GATE: R62.2, U8.6 (QG)
SW8: D3.1 (K), H2.16, R55.1, U14.4 (-)
SW8GATE: R50.2, U8.7 (QH)
SW9: D9.1 (K), H2.17, R91.1, U20.4 (-)
SW9GATE: R86.2, U9.15 (QA)
SW10: D6.1 (K), H2.18, R73.1, U17.4 (-)
SW10GATE: R68.2, U9.1 (QB)
TELEM_I3V3: R32.1, U2.19 (I12), U11.2 (OUT)
TELEM_I5V: R30.1, U2.20 (I11), U10.2 (OUT)
TELEM_IBATV: R16.1, U2.21 (I10), U7.2 (OUT)
TELEM_ISW1: U2.9 (I0), U18.1
TELEM_ISW2: U2.8 (I1), U12.1
TELEM_ISW3: U2.7 (I2), U13.1
TELEM_ISW4: U2.6 (I3), U15.1
TELEM_ISW5: U2.5 (I4), U19.1
TELEM_ISW6: U2.4 (I5), U21.1
TELEM_ISW7: U2.3 (I6), U16.1
TELEM_ISW8: U2.2 (I7), U14.1
TELEM_ISW9: U2.23 (I8), U20.1
TELEM_ISW10: U2.22 (I9), U17.1
TELEM_TBRD: R1.2, TH1.1, U1.18 (I13)
TELEM_V3V3: R36.2, R37.1, U1.19 (I12)
TELEM_V5V: R34.2, R35.1, U1.20 (I11)
TELEM_VBATV: R18.2, R19.1, U1.21 (I10)
TELEM_VSW1: R77.2, R78.1, U1.9 (I0)
TELEM_VSW2: R41.2, R42.1, U1.8 (I1)
TELEM_VSW3: R47.2, R48.1, U1.7 (I2)
TELEM_VSW4: R59.2, R60.1, U1.6 (I3)
TELEM_VSW5: R83.2, R84.1, U1.5 (I4)
TELEM_VSW6: R95.2, R96.1, U1.4 (I5)
TELEM_VSW7: R65.2, R66.1, U1.3 (I6)
TELEM_VSW8: R53.2, R54.1, U1.2 (I7)
TELEM_VSW9: R89.2, R90.1, U1.23 (I8)
TELEM_VSW10: R71.2, R72.1, U1.22 (I9)
VCC: C22.1, C23.1, C31.1, C32.1, C33.1, C34.1, C35.1, C36.1, C37.1, C38.1, C39.1, C40.1, C41.1, C42.1, R13.1, R14.1, R24.1, R25.1, R26.1, R27.1, U5.2 (VO), U7.1 (Vcc), U10.1 (Vcc), U11.1 (Vcc), U12.5 (V+), U13.5 (V+), U14.5 (V+), U15.5 (V+), U16.5 (V+), U17.5 (V+), U18.5 (V+), U19.5 (V+), U20.5 (V+), U21.5 (V+)
VDD: C1.1, C3.1, C8.1, C9.1, C10.1, C11.1, C12.1, C24.1, C30.1, J1.1, JP1.3 (B), Q2.5 (D), Q2.6 (D), Q2.7 (D), Q2.8 (D), R7.1, R8.1, R9.1, U1.24 (VCC), U2.24 (VCC), U4.1 (VBAT), U4.9 (VDDA), U4.24 (VDD), U4.36 (VDD), U4.48 (VDD), U8.10 (~SRCLR), U8.16 (VCC), U9.10 (~SRCLR), U9.16 (VCC)
VUSB: H1.32, J2.9, J2.10

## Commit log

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2021-12-20 Cell level and pack level protections, and charge balancing
    [BatteryMaster.sch, Cell.sch, MPPT.sch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]
2021-12-20 add vbat and ibat telemetry read
    [BatteryMaster.sch]
2021-12-21 add battery temperature telemetry and heaters
    [BatteryMaster.sch, Cell.sch, Heater+Thermistor.sch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]
2021-12-22 revamp solar conditioning, use lt3652 instead of homebrew buck converter
    [BatteryMaster.sch, Cell.sch, MPPT.sch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]
2021-12-22 Spec out switching controllers for PCMs
    [BatteryMaster.sch, Cell.sch, Heater+Thermistor.sch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]
2021-12-23 Finish components for buck converters, add UVLO feature, correct all mosfet orientations
    [BatteryMaster.sch, Heater+Thermistor.sch, PowerConditioning.sch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]
2021-12-23 Finish speccing out components for 12V boost
    [MPPT.sch, PowerConditioning.sch, SolarConditioning.sch]
2021-12-24 Remove zeners, add PDMs, correct MPPT setpoint controller
    [12VPD.sch, BatteryMaster.sch, Cell.sch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]
2021-12-24 Cleanup, add yellow fill to symbols, add MAX4373
    [12VPD.sch, Cell.sch, PowerConditioning.sch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]
2021-12-24 astable 555 boost concept
    [555 boost converter.kicad_pcb, 555 boost converter.sch]
2021-12-24 rearrange the stack headers to make some damn sense *looks at clydespace*
    [BatteryMaster.sch, Cell.sch, Heater+Thermistor.sch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]
2021-12-25 spec out new cell protection IC and mosfets, figured out current limit calculation
    [555 boost converter.sch, BatteryMaster.sch, Cell.sch]
2021-12-26 Add OCP, resize some sheets
    [BatteryMaster.sch, Cell.sch, PowerConditioning.sch]
2021-12-29 fix the bidirectional ocp to actually be bidirectional
    [BatteryMaster.sch]
2021-12-30 start placing battery telemetry node
    [BatteryMaster.sch]
2021-12-31 bidirectional inhibits, remove unrealistic zener, replace all irf7425 with irf7458
    [BatteryMaster.sch, Cell.sch, Heater+Thermistor.sch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]
2021-12-31 add programming to micro
    [BatteryMaster.sch, SolarConditioning.sch]
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2022-01-01 Fourth BCR, with boost stage
    [555 boost converter.kicad_pcb, 555 boost converter.sch, 555Boost.sch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]
2022-01-02 Connect PDMs, add stm32 on eps board, add bcrout current telemetry, improve spacing
    [MPPT.sch, PDM12V.sch, PDM3V3.sch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]
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2022-01-02 add comments and titles
    [BatteryMaster.sch, Cell.sch, Heater+Thermistor.sch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]
2022-01-02 Add USB charge to BCR3B
    [Boost-BuckMPPT.sch, SolarConditioning.sch]
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2022-01-04 implement a retry timer
    [BatteryMaster.sch, Boost-BuckMPPT.sch, Cell.sch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]
2022-01-04 fix a minor wire mixup
    [PowerConditioning.sch]
2022-01-04 connect retry timers, organize sheet
    [PowerConditioning.sch, RetryTimer.sch]
2022-01-04 Correct watchdog implementation
    in case of a latchup event, reset pin wouldn't work. need to cycle power to chip
    [BatteryMaster.sch, TJ-EPS.sch]
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2022-01-05 Implement pulse resets
    [PowerConditioning.sch, Pulse+RetryTimer.sch, PulseGenerator.sch]
2022-01-05 Replace tantalums with MLCCs
    [PowerConditioning.sch]
2022-01-05 get rid of series capacitors
    [BatteryMaster.sch, Cell.sch, Pulse+RetryTimer.sch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]
2022-01-05 add solar telemetry sheet
    [BatteryMaster.sch, Boost-BuckMPPT.sch, Cell.sch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]
2022-01-06 Implement solar telemetry, add a sheet layout
    [BatteryMaster.sch, Boost-BuckMPPT.sch, Cell.sch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]
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2022-01-08 Add PDM control using shift registers
    [PowerDistribution.sch, TJ-EPS.sch]
2022-01-08 Annotate and begin adding footprints
    [BatteryMaster.sch, Boost-BuckMPPT.sch, Cell.sch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]
2022-01-09 add some more footprints
    [Boost-BuckMPPT.sch, Heater+Thermistor.sch, MPPT.sch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]
2022-01-10 Add all IC footprints
    [BatteryMaster.sch, Boost-BuckMPPT.sch, Heater+Thermistor.sch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]
2022-01-11 add cell protection concept, make the protection board integrated into main board
    consider removing cell level protection and relying on integrated cell protection
    [Cell.kicad_pcb, Cell.sch]
2022-01-12 add a bunch of cap and shunt resistor footprints
    [BatteryMaster.sch, Boost-BuckMPPT.sch, Heater+Thermistor.sch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]
2022-01-12 Remove cell level protections, rely on 18650 internal protections
    [BatteryMaster.sch, Cell.kicad_pcb, Cell.sch]
2022-01-13 Major descope, remove 12V boost and all related circuitry
    [BatteryMaster.sch, Boost-BuckMPPT.sch, Heater+Thermistor.sch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]
2022-01-13 Update stack header pinouts and re-annotate
    [BatteryMaster.sch, Boost-BuckMPPT.sch, Heater+Thermistor.sch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]
2022-01-13 Get rid of unused sch files
    [Cell.sch, PDM.sch, PDM12V.sch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]
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2022-01-14 Despec inductor for buck converters, finish adding footprints, general schematic cleanup
    [Boost-BuckMPPT.sch, MPPT.sch, PowerConditioning.sch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]
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2022-01-14 Fix two different +BATT labels causing batbus to be connected to raw battv
    [BatteryMaster.sch, TJ-EPS.kicad_pcb]
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2022-01-14 Split up into 3 projects for separate boards
    [BatteryMaster.kicad_pcb, BatteryMaster.sch, Boost-BuckMPPT.sch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]
2022-01-14 Add standard dimensions to batt
    TODO: replace footprint of 18650
    [BatteryMaster.kicad_pcb, BatteryMaster.sch, Boost-BuckMPPT.sch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]
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2022-01-27 replace stack header footprint
    [TJ-EPS.kicad_pcb, TJ-EPS.sch]
2022-01-28 swd with debug, and replace boot jumper with solder jumper
    [BatteryMaster.kicad_pcb, BatteryMaster.sch, Heater+Thermistor.sch]
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2022-01-29 Finish laying out battery pcb v1, now time for revisions
    [BatteryMaster.kicad_pcb]
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2022-01-29 Round off some corners and set up eps board for routing
    [BatteryMaster-B_Cu.gbr, BatteryMaster-B_Mask.gbr, BatteryMaster-B_Paste.gbr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]
2022-02-01 Replace EVERY LT6106 with INA180A3
    Friendship ended with LT6106
    now ina180 is my best friend
    [Boost-BuckMPPT.sch, MPPT.sch, PDM3V3.sch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]
2022-02-01 change some power flags for latchup prevention
    [BatteryMaster.kicad_pcb, Heater+Thermistor.sch, PowerDistribution.sch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]
2022-02-01 4 layer + fix pdm gate SRs
    [PDM3V3.sch, TJ-EPS.kicad_pcb]
2022-02-02 route some stuff, realize 0603 is probably necessary
    [TJ-EPS.kicad_pcb]
2022-02-02 dunno what happened here but I'll go with it
    [PDMBATV.sch, PowerDistribution.sch, TJ-EPS.sch]
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2022-02-14 correct setpoint circuitry
    [Boost-BuckMPPT.sch, MPPT.sch]
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2022-03-21 correct layout
    [Boost-BuckMPPT.kicad_sch, SolarConditioning.kicad_sch, TJ-EPS.kicad_pcb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]
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2022-03-26 minor fixes
    [BatteryMaster.kicad_sch, PowerConditioning.kicad_sch, TJ-EPS.kicad_sch]
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2022-03-26 descope to 10 pdms, replace mcp3208 with mcp3008 bc of stock
    [PowerConditioning.kicad_sch, SolarConditioning.kicad_sch, TJ-EPS.kicad_sch]
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2022-03-28 remove flex pcb, move to battery board
    [BatteryMaster.kicad_pcb, BatteryMaster.kicad_sch, Cell.kicad_sch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]
2022-03-28 push rev 2 (no more silly numbering conventions)
    [BatteryMaster.kicad_sch, Boost-BuckMPPT.kicad_sch, Heater.kicad_sch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]
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2022-04-01 This is more crowded than it needs to be
    [BatteryMaster.kicad_pcb, BatteryMaster.kicad_sch]
2022-04-01 move solar to daughterboard... again. Also replace all 0603 resistor with 0805
    [BatteryMaster.kicad_pcb, BatteryMaster.kicad_sch, Boost-BuckMPPT.kicad_sch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]
2022-04-03 Micro + PCM blocks
    Micro + PCM blocks
    [PDM.kicad_sch, Pulse+RetryTimer.kicad_sch, TJ-EPS.kicad_pcb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]
2022-04-04 Revert "Micro + PCM blocks"
    This reverts commit bd53ca95fb26b4e6798500a23db46c8297649bcb.
    [PDM.kicad_sch, Pulse+RetryTimer.kicad_sch, TJ-EPS.kicad_pcb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]
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2022-04-05 simplify reset and retry
    [BatteryMaster.kicad_sch, PDM.kicad_sch, PowerConditioning.kicad_sch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]
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2022-04-09 Route stack header past switches
    Route stack header past switches
    [TJ-EPS.kicad_pcb]
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2022-04-10 flip PDM current monitors
    [Boost-BuckMPPT.kicad_sch, MPPT.kicad_sch, PDM.kicad_sch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]
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2022-04-13 Switch telem and switching
    Switch telem and switching
    [TJ-EPS.kicad_pcb]
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2022-04-20 revert kiran's mistake
    [TB9061AFNG,EL.stp, rxnWheel.kicad_pcb, rxnWheel.kicad_sch]
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2022-04-22 Move silkscreen off of vias and MILESTONE V1 COMPLETE
    [SolarConditioning.kicad_pcb, SolarConditioning.kicad_sch]
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
